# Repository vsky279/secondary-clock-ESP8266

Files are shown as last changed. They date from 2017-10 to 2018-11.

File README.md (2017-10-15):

# Driving secondary clock by ESP8266

Check out this Youtube [video](http://www.youtube.com/watch?v=zKabXwngn9Y) to see the clock in work.

Secondary clock IPJ0612 driven by ESP8266 (http://www.youtube.com/watch?v=zKabXwngn9Y)

## Intro

I have received this beautiful secondary clock [IPJ0612](https://www.pragotron.sk/?ukaz=content/ipj0612) produced by Czech company Pragotron in 80's. Secondary here means that the clock is only a "display" and has to receive signals from a central clock to move by one minute.
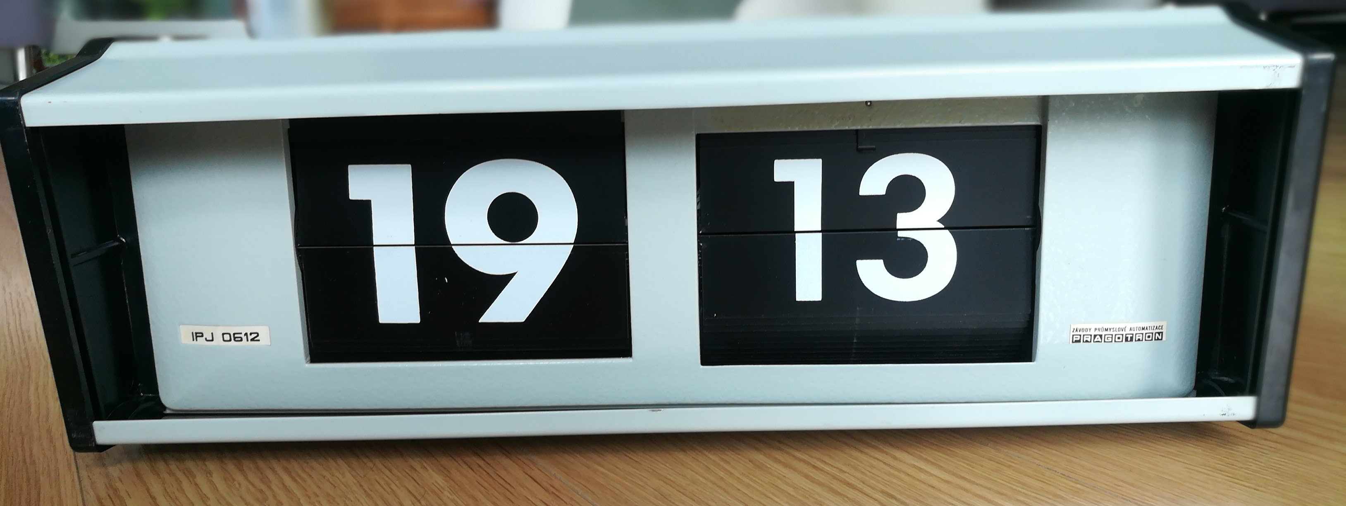
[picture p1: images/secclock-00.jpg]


The clock is driven by kind of a stepper motor, powered by 24V. It has two wires as input directly connected to the coil. For one half turn an impulse of 24V is required for the remaining half turn -24V are applied.
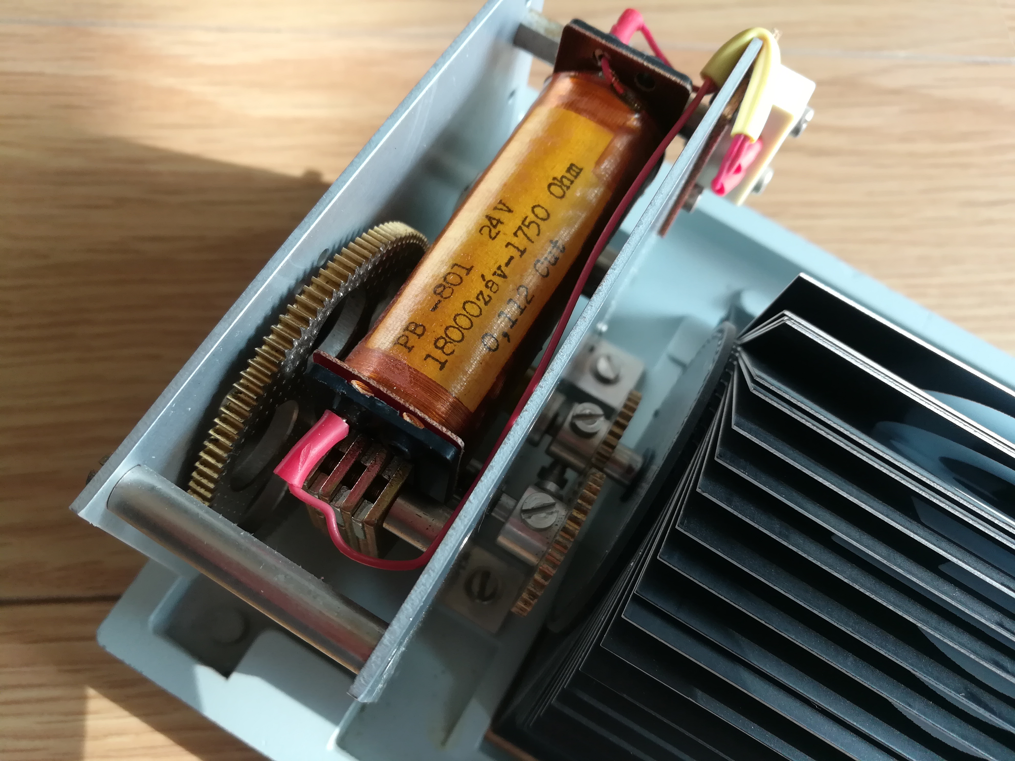
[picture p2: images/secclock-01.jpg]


## Electronics

We needed to use a circuit that can revert the voltage on its output. Two inputs are connected to ESP8266 GPIOs (GPIO0 and GPIO2). GPIO0 set to high makes 24V on output. Setting GPIO2 high causes -24V on output. A pull-up resistors are connected to GPIOs so that ESP8266 boots in desired 'normal operation' mode. A protection transistor (QX on the scheme) for accidental highs on both inputs has been added. The ESP8266 ESP-01 version is used.

We have used Eagle to draw the [scheme](./hw/driver.sch) and design the [board](./hw/board.sch).
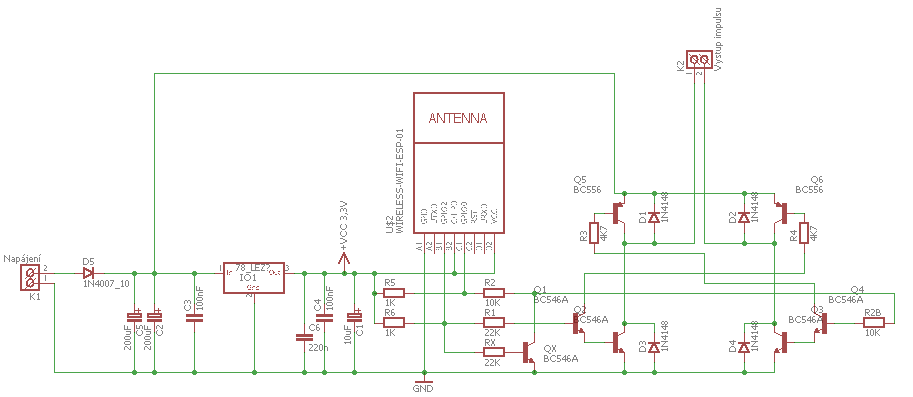
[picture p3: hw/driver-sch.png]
scheme

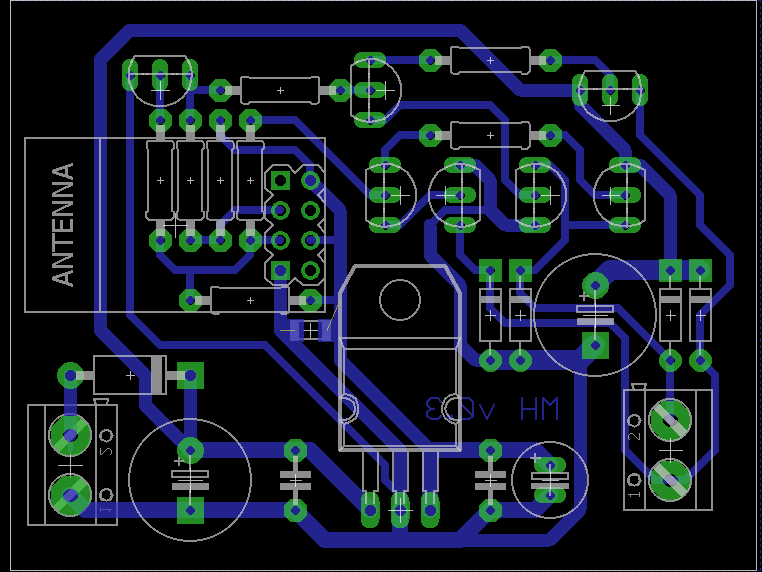
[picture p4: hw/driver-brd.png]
board


To get the 3.3 voltage to power the ESP8266 a LM1085IT-3.3 TO220 regulator is used.
In my implementation, I'm using step-down module as I had one spare at home (the component with annoying blue LED on the pictures below). It's sold on eBay and can be found as [3A 9V/12V/19V To 3.3V DC-DC USB Step Down Buck Power Supply Module For Car](https://www.ebay.com/sch/i.html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). 

## Programming

I am using NodeMCU Lua ([https://github.com/nodemcu/nodemcu-firmware](https://github.com/nodemcu/nodemcu-firmware)) to program the ESP8266. The programming in Lua is very easy so the core program can have less than 140 lines including the web server used to adjust the clock.

A [NodeMCU custom builds](https://nodemcu-build.com/) tool can be used to compile the binary for ESP8266. Beside standard modules the following modules are used: `cron, enduser_setup, rtctime, sntp`. I have used the integer version of the firmware is used. Though float version should be fine too.

I am using [ESP8266 Flasher](https://github.com/nodemcu/nodemcu-flasher) to flash the binary.

To upload Lua files and files used by the web server the [ESPlorer](https://esp8266.ru/esplorer/) GUI can be used.

The program connects to the WIFI, regularly synchronizes time via NTP and sends 300ms to GPIO0 and GPIO1 alternately. To show correct time ESP needs to know what time the clock is showing at startup so it can set it to actual time. This can be adjusted in web browser as the ESP8266 is running a web server. Otherwise the clock assumes correct time is displayed and sends signals as time goes on.

It exposes also a telnet server so an OTA-like update of Lua codes can be performed.

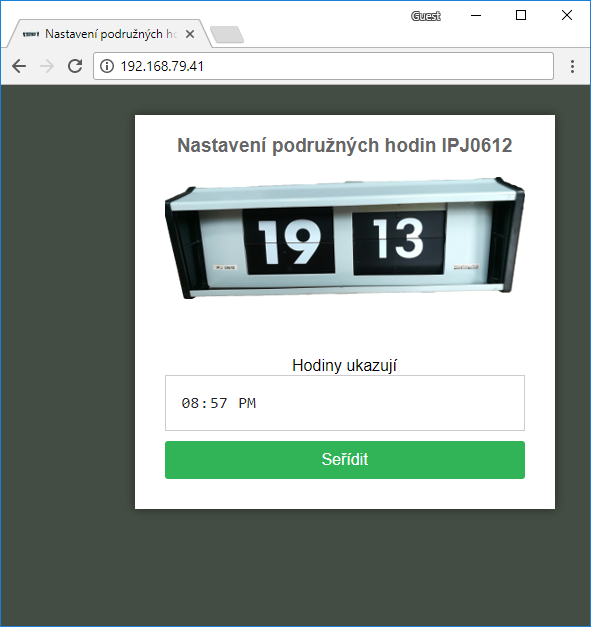
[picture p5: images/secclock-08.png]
web server


In my implementation am using only 18V to run the clock (a power adapter from an old printer). With 24V the signal could probably be shorter than 300ms so clock adjustment would be faster.

The source code is in the folder [lua_code](https://github.com/vsky279/secondary-clock-ESP8266/tree/master/lua_code).

## Assembly

A 3d printed [holder](./holder/holder.skp) (designed in SketchUp) and double face duck tape has been used to mount the board inside the clock. An [STL file](./holder/holder.stl) is usually used in the slicer software.
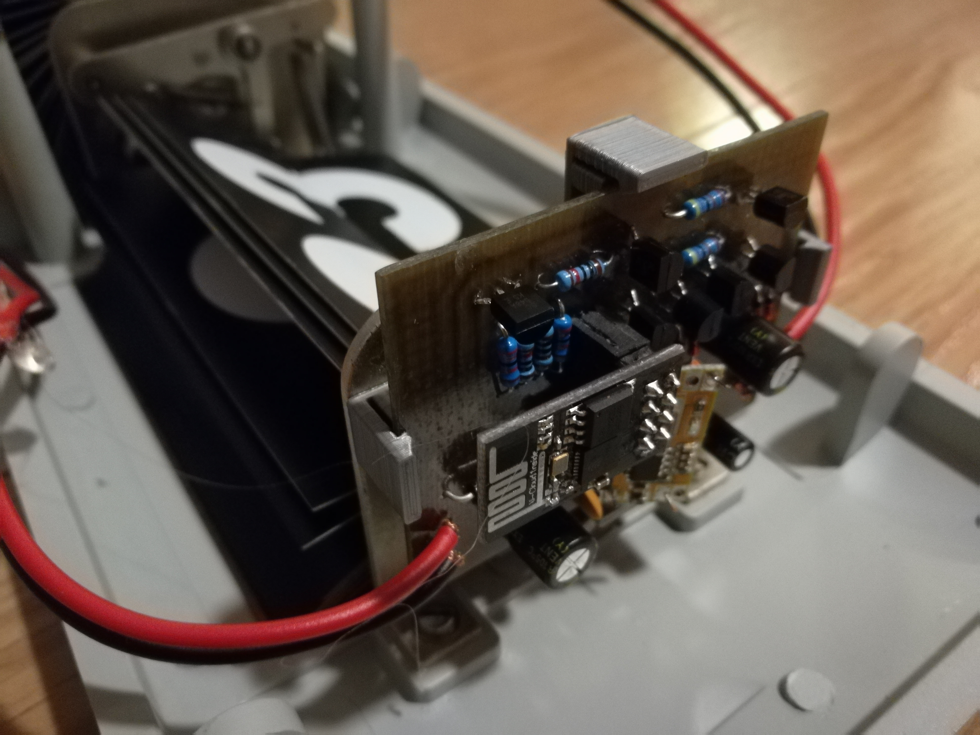
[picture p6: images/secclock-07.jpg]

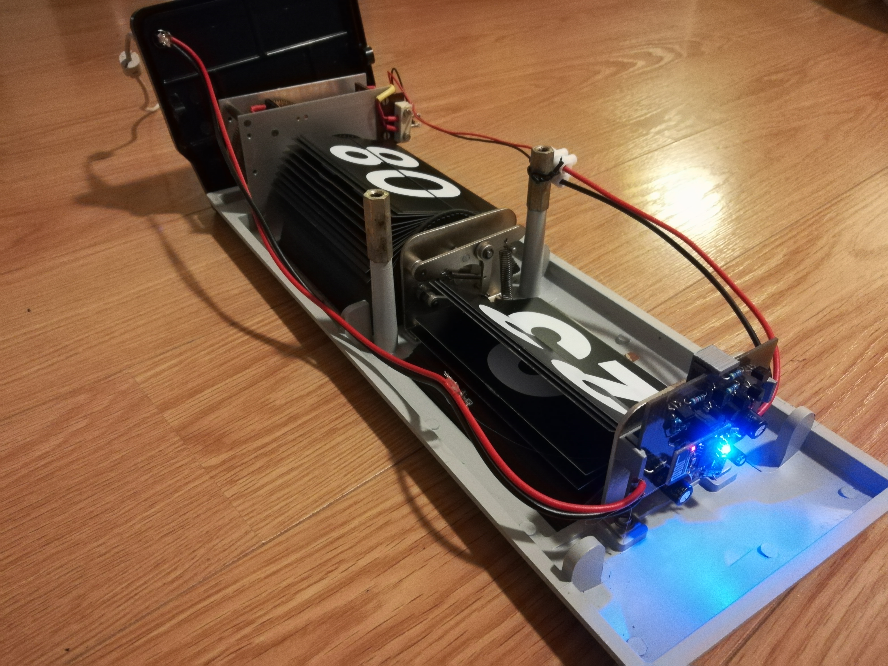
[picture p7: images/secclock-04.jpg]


I have also designed a cap to cover the hole of the original connector ([SketchUp file](./hw/holder/cap.skp) and [STL file](./holder/cap.stl)) - not shown on any of photos.

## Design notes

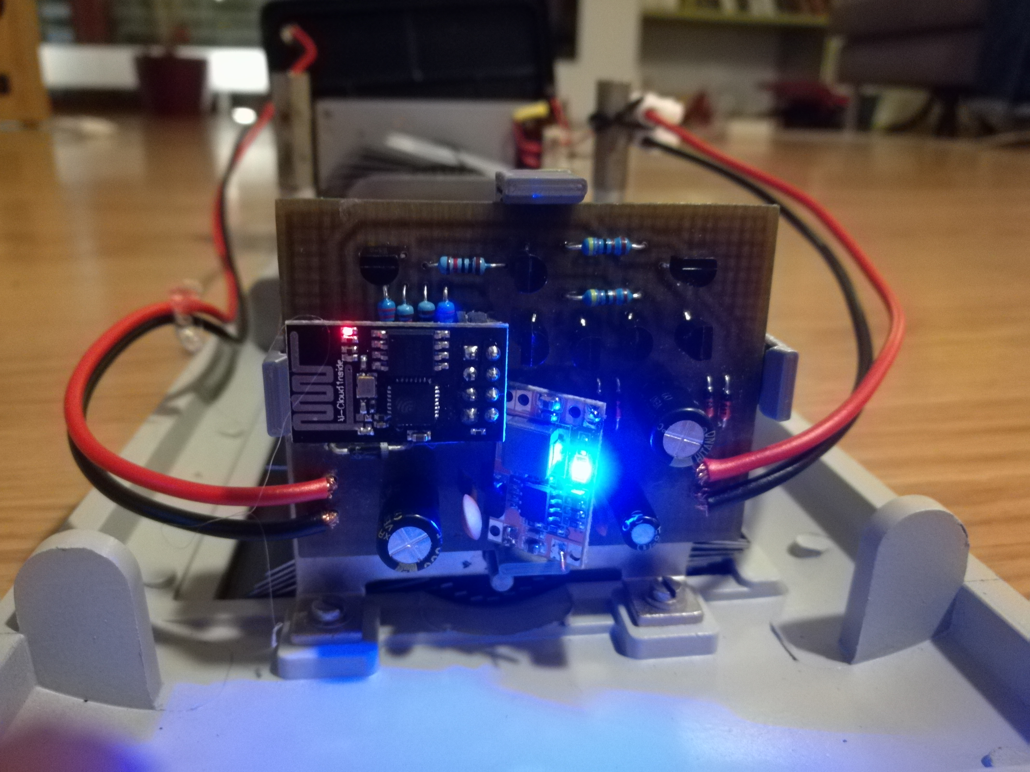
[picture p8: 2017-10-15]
images/secclock-05.jpg

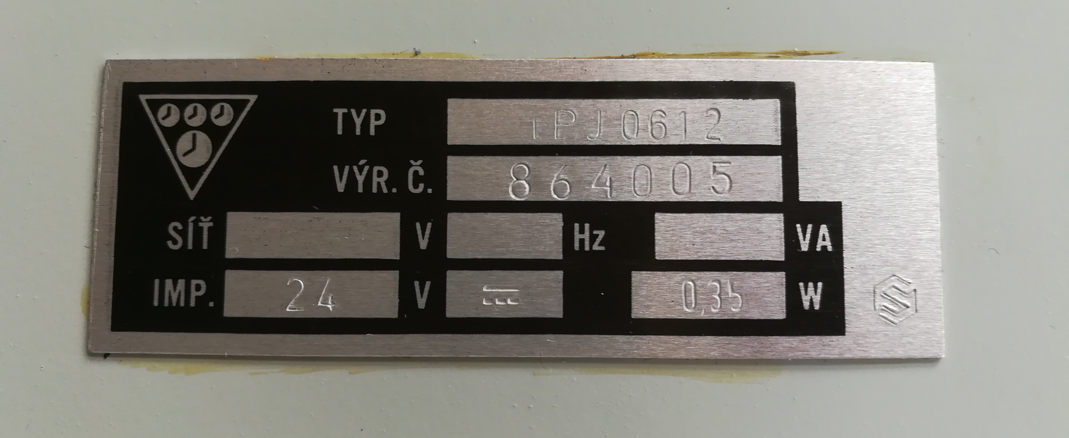
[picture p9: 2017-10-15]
images/secclock-03.jpg

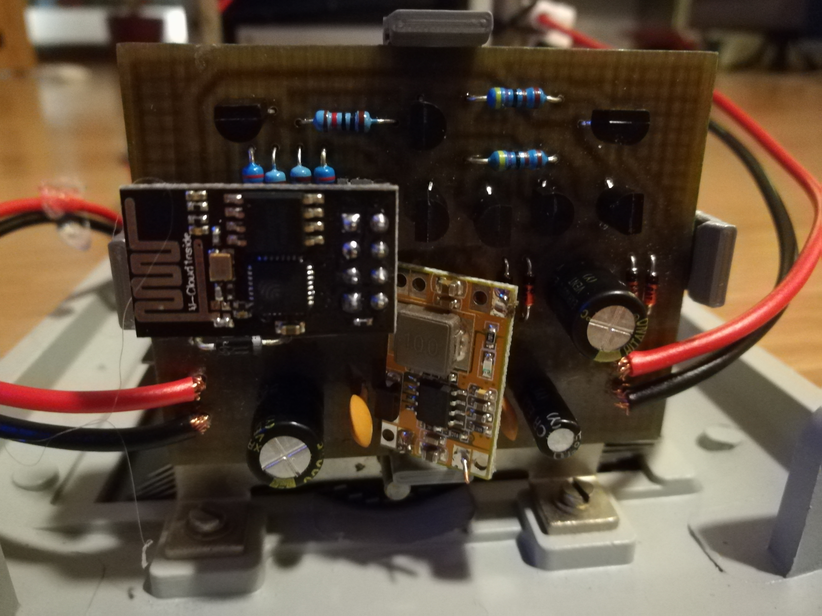
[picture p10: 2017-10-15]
images/secclock-06.jpg

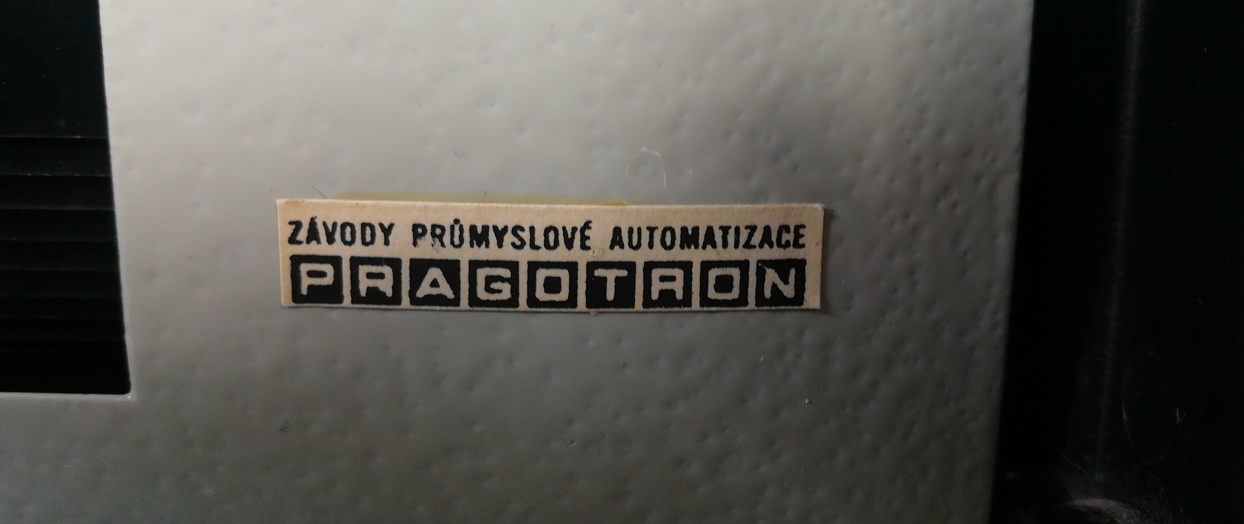
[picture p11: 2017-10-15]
images/secclock-02.jpg

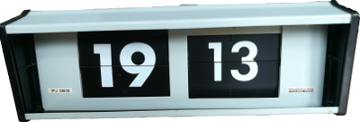
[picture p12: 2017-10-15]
lua_code/src/IPJ_0612-orig.png

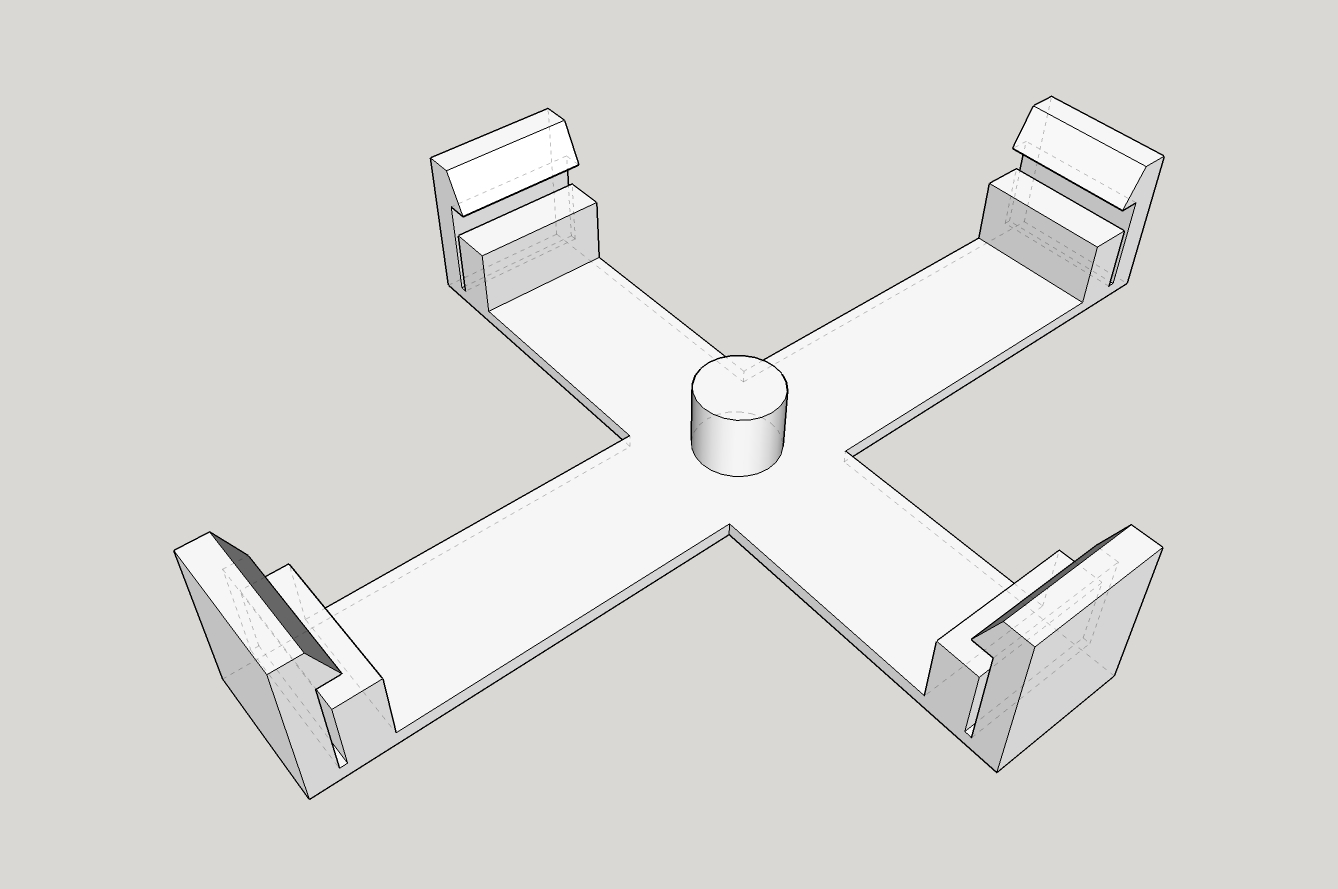
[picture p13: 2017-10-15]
holder/holder.jpg

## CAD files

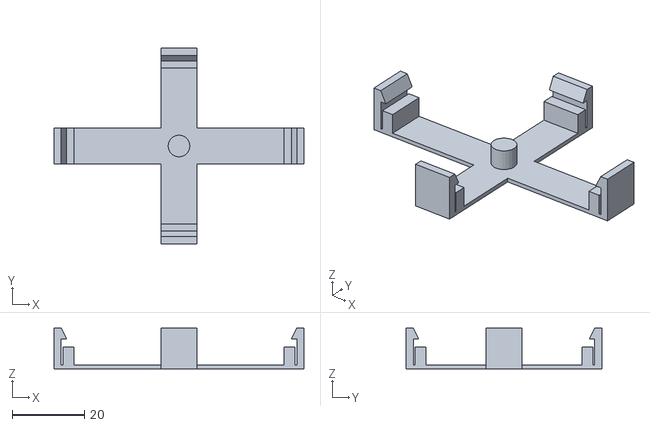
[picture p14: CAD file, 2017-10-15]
holder/holder.stl
69.0 x 54.0 x 11.2

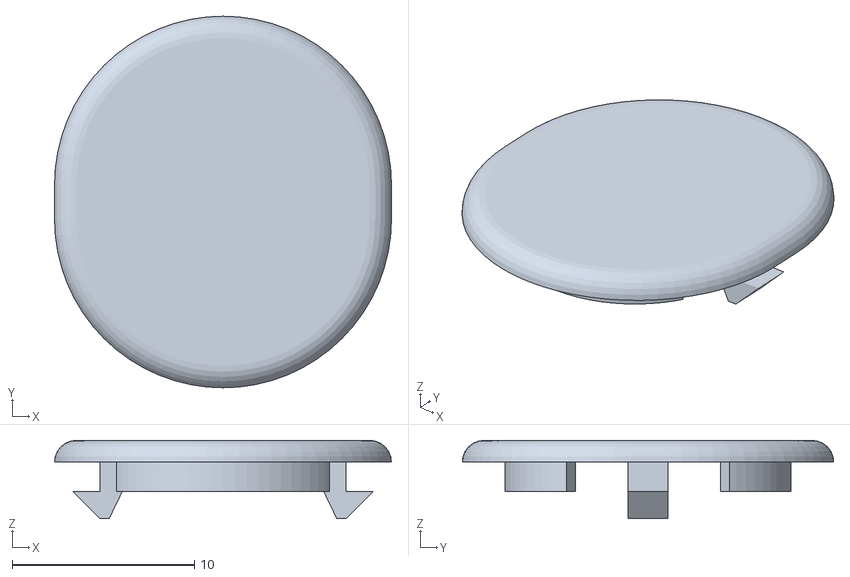
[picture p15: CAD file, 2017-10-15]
holder/cap.stl
18.5 x 20.4 x 4.30

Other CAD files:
holder/cap.skp
holder/holder.skp

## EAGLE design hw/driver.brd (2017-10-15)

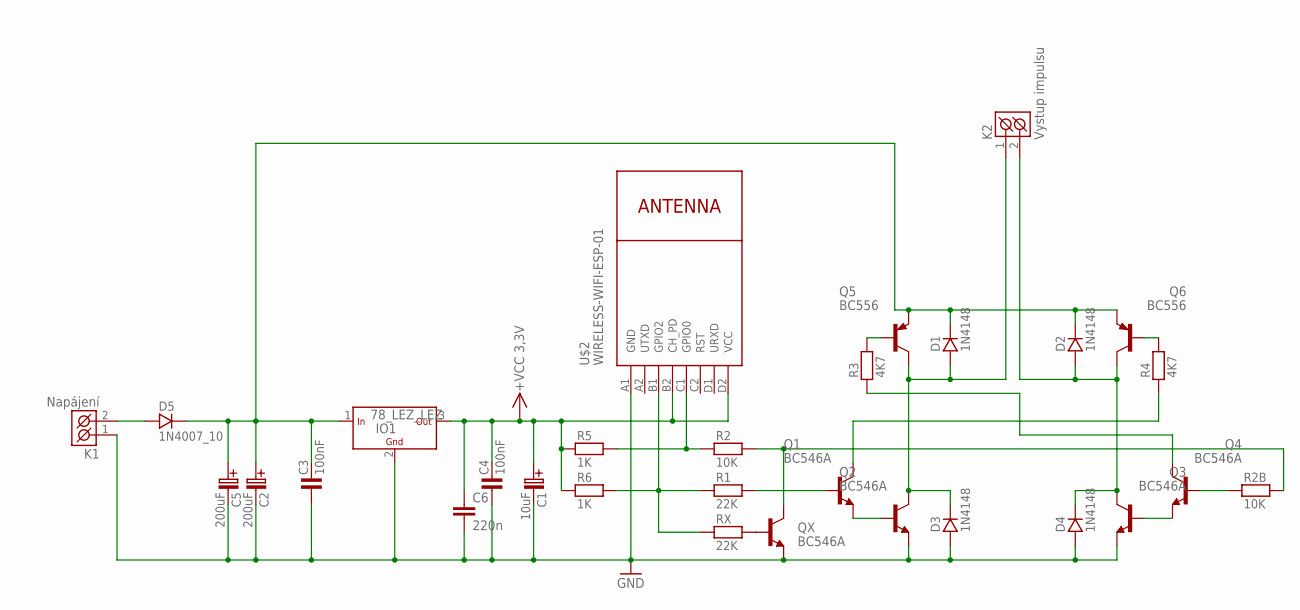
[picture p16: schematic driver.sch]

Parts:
C1: 10uF; C-EL_2,5
C2, C5: 200uF; C-EL_5
C3, C4: 100nF; C-5
C6: 220n; C1206
D1, D2, D3, D4: 1N4148; DO35
D5: 1N4007_10; DO41
IO1: 78_LEZ_LEZ; TO-220
K1: Napájení; CZM_5/2
K2: Vystup impulsu; CZM_5/2
Q1, Q2, Q3, Q4: BC546A; TO92-EBC
Q5, Q6: BC556; TO92-EBC
QX: BC546A; TO92-EBC
R1: 22K; R-10
R2, R2B: 10K; R-10
R3, R4: 4K7; R-10
R5, R6: 1K; R-10
RX: 22K; R-10
U$2: WIRELESS-WIFI-ESP-01

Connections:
GND: C1.C- (C_EL-), C2.C- (C_EL-), C3.1, C4.1, C5.C- (C_EL-), C6.2, D3.A, D4.A, IO1.2 (GND), K1.1 (K1), Q2.E, Q3.E, QX.E, U$2.A1 (GND)
unnamed: D2.A, D4.K, K2.2 (K2), Q3.C, Q6.C
unnamed: D1.A, D3.K, K2.1 (K1), Q2.C, Q5.C
unnamed: C2.C+ (C_EL+), C3.2, C5.C+ (C_EL+), D1.K, D2.K, D5.K, IO1.1 (IN), Q5.E, Q6.E
unnamed: Q5.B, R3.2
unnamed: Q6.B, R4.2
unnamed: Q4.C, R3.1
unnamed: Q1.C, R4.1
unnamed: Q4.B, R2B.1
unnamed: Q3.B, Q4.E
unnamed: Q1.E, Q2.B
unnamed: D5.A, K1.2 (K2)
unnamed: Q1.B, R1.2
unnamed: R1.1, R6.2, RX.1, U$2.B1 (GPIO2)
unnamed: QX.C, R2.2, R2B.2
unnamed: R2.1, R5.2, U$2.C1 (GPIO0)
unnamed: QX.B, RX.2
VCC: C1.C+ (C_EL+), C4.2, C6.1, IO1.3 (OUT), R5.1, R6.1, U$2.B2 (CH_PD), U$2.D2 (VCC)

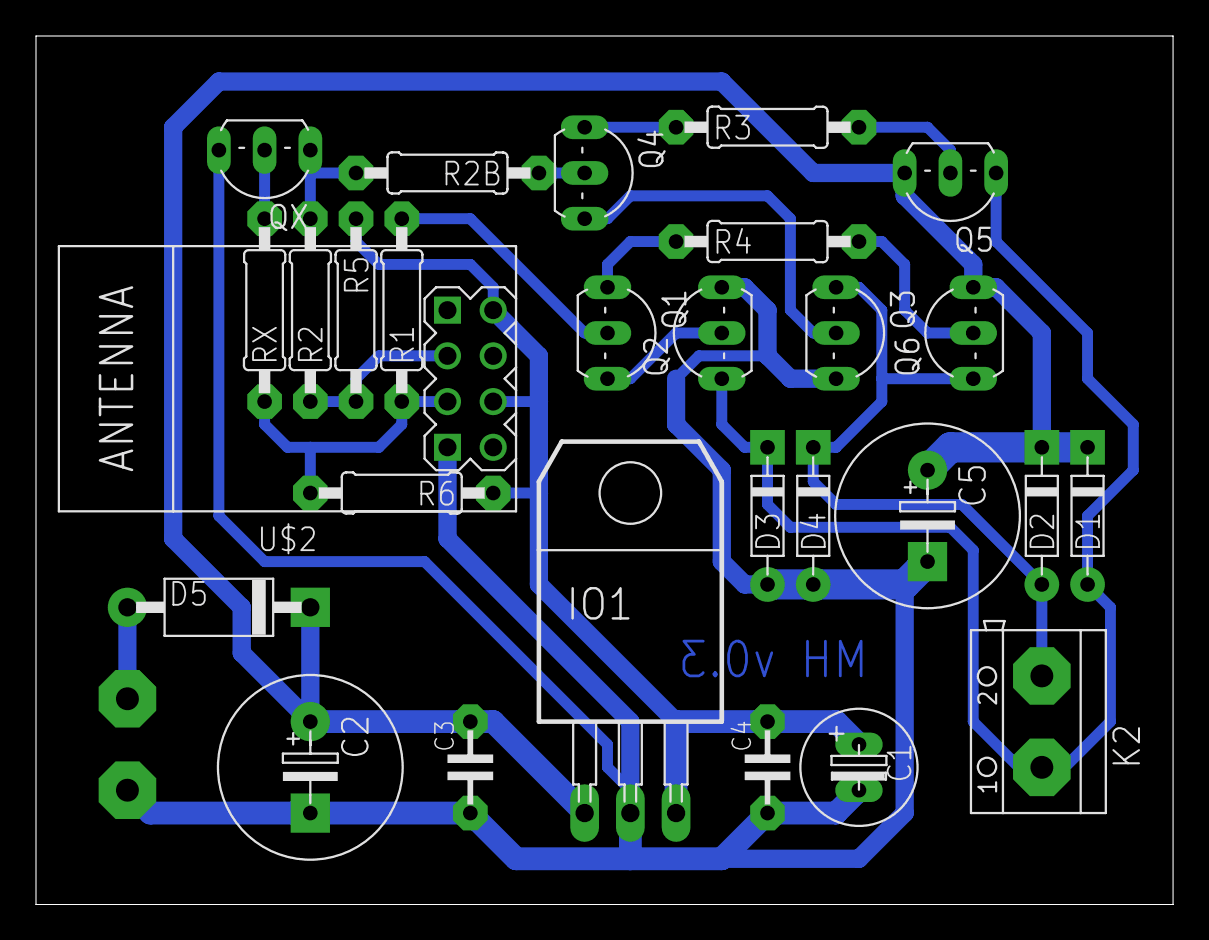
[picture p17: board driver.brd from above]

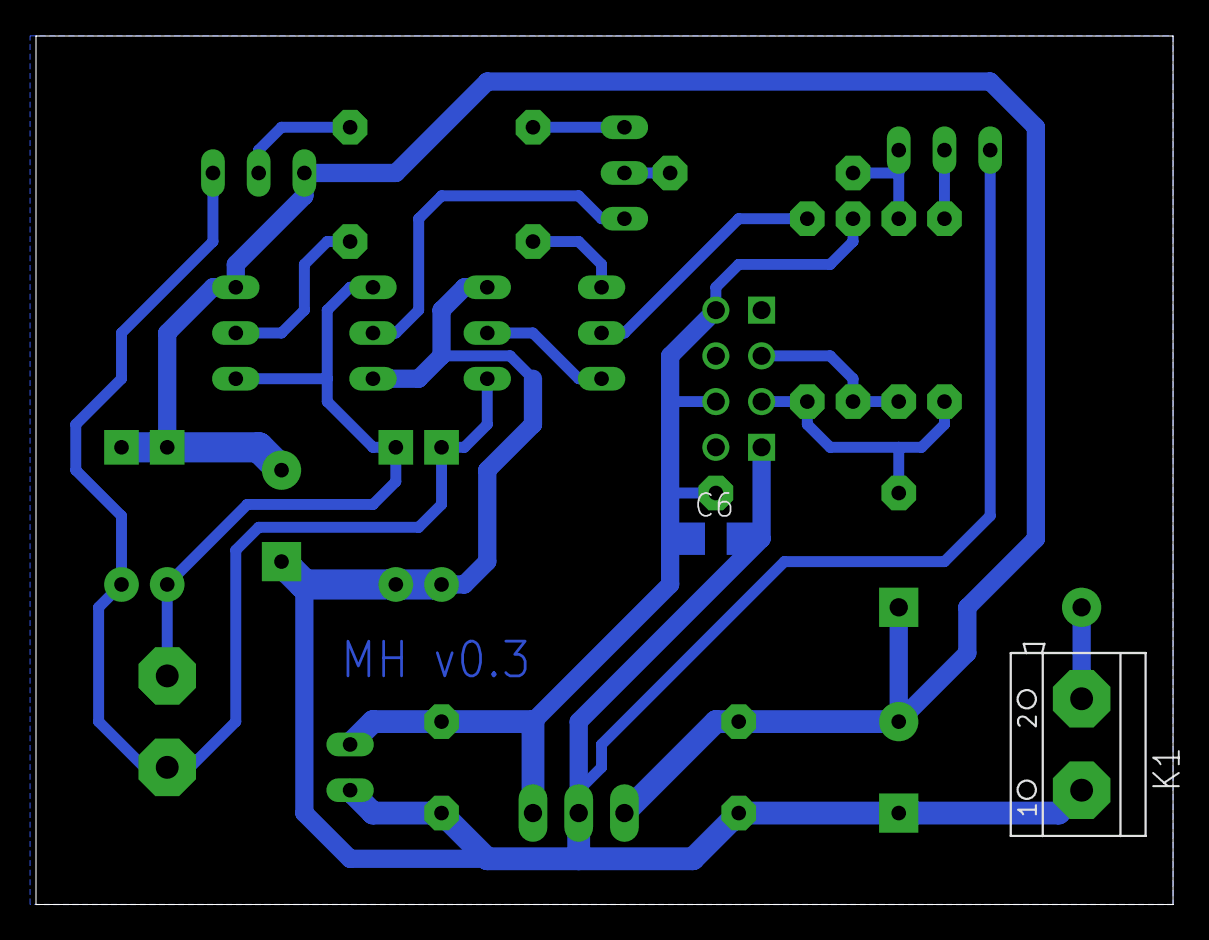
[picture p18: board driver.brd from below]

Board: 2 copper layers, 63.2 x 48.2 mm, 30 parts (2 on the bottom side), 18 nets.

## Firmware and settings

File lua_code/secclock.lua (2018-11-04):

n=require("ntp")

local PIN1 = 3
local PIN2 = 4
local impulse = 300 -- in ms
local delay = 10 -- in ms

local tmr_alarm, tmr_unregister, tmr_ALARM_SINGLE, tmr_ALARM_AUTO, tmr_create, tmr_now = tmr.alarm, tmr.unregister, tmr.ALARM_SINGLE, tmr.ALARM_AUTO, tmr.create, tmr.now
local string_find, string_gmatch, string_format, string_sub, string_gsub = string.find, string.gmatch, string.format, string.sub, string.gsub
local gpio_mode, gpio_serout, gpio_write, gpio_HIGH, gpio_LOW, gpio_OUTPUT = gpio.mode, gpio.serout, gpio.write, gpio.HIGH, gpio.LOW, gpio.OUTPUT

--display == (19*60+15) * 60

local state = true
local tmr_sync = tmr_create()
local tmr_adjust = tmr_create()
local tmr_zero = tmr_create()

gpio_mode(PIN1, gpio_OUTPUT)
gpio_mode(PIN2, gpio_OUTPUT)
gpio_write(PIN1, gpio_LOW)
gpio_write(PIN2, gpio_LOW)

local function display_s()
  local minute = display / 60
  local hour = minute / 60
  minute = minute % 60
  return string_format("%02d:%02d", hour, minute)
end

local last_step = 0
function step()
  local now = tmr_now()
  local dif = now - last_step
  dif = ( (dif < 0) and ((dif + 0x7FFFFFFE) + 1) or dif) /1000 -- workaround for #1691
  if dif < (impulse + delay) then return end

  local pin = state and PIN1 or PIN2
  state = not state
  display = (display + 60) % 86400
  print(string_format("display shows %s, signal on GPIO%d (free mem: %d)", display_s(), pin, node.heap()))
  --gpio_serout(pin, gpio_HIGH, {impulse*1000, delay*1000}, 1, 1)
  gpio_write(pin, gpio_HIGH)
  tmr_alarm(tmr_zero, impulse, tmr_ALARM_SINGLE, function() return gpio_write(pin, gpio_LOW) end)
  last_step = now
end

function adjust()
  local now = n:time() % 86400
  local dif = (now - display) / 60 -- difference in minutes
  if dif < -10 then dif = dif + 1440 end

  print(string_format("display shows %s, time is %s, %d minutes difference (free mem: %d)", display_s(), n:format(now), dif, node.heap()))
  if dif > 0 then
    step()
    dif = dif - 1
    if dif > 0 then
      tmr_alarm(tmr_adjust, impulse + delay, tmr_ALARM_SINGLE, adjust)
    end
  end
end

local cronent
function timeSync()
    n:sync(function ()
      if not display then display = ((n:time() % 86400) / 60) * 60 end
      if not cronent then cronent = cron.schedule("* * * * *", adjust) end
      return tmr_alarm(tmr_sync, 90*60*1000, tmr_ALARM_AUTO, timeSync) 
    end, function() 
      return tmr_alarm(tmr_sync, 10*1000, tmr_ALARM_SINGLE, timeSync) 
    end)
end

timeSync()

srv=net.createServer(net.TCP)
srv:listen(80,function(conn)
  conn:on("receive", function(client, request)
    local _, _, method, path, vars = string_find(request, "([A-Z]+) (.+)?(.+) HTTP")
    if(method == nil)then
        _, _, method, path = string_find(request, "([A-Z]+) (.+) HTTP")
    end
    print("request: ", method, path, vars)
    path = string_sub(path, 2) -- remove first char, i.e. "/"
    local index = (path == "")
    path = index and "index.html" or path
    local fd = file.open(path, "r")
    if not fd then 
        client:send("HTTP/1.0 404 Not Found\r\n\r\n404 Not Found\r\n") 
        return
    end
    if index then
      local _GET = {}
      if (vars ~= nil)then
          for k, v in string_gmatch(vars, "(%w+)=([%w%%]+)&*") do
            _GET[k] = v
          end
      end
      local _GET_time = _GET.time
      _GET = nil
      if(_GET_time) then
        local _, _, hour, minute = string_find(_GET_time, "([0-9]+)%%3A([0-9]+)")
        print(string_format("set time to: %02d:%02d", hour, minute))
        display = hour*3600+minute*60
        adjust()
      end

      local line, content = "", ""
      while line do
          line = string_gsub(line, "$TIME", display_s())
          content = content .. line
          line = fd:readline()
      end
      fd:close()
      if content then 
        client:send(content, function (c) 
          c:close() 
          c:on("sent", nil)
        end) 
      end
    else
      local function sendfile()
        local line=fd:read(1024)
        if line then
          client:send(line, sendfile)
        else
          fd:close()
          client:close()
          client:on("sent", nil)
        end
      end
      sendfile()
    end
  end)
end)

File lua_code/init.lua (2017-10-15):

local fn="secclock"
local smph = "semaphore.tmp"

local tmr_create, tmr_alarm, tmr_ALARM_SINGLE = tmr.create, tmr.alarm, tmr.ALARM_SINGLE

gpio.mode(3, gpio.OUTPUT);
gpio.write(3, gpio.LOW);
gpio.mode(4, gpio.OUTPUT);
gpio.write(4, gpio.LOW);

local function con(t)
  local cred = {your_default_wifi="password"}
  for ssid, _ in pairs(t) do
    if cred[ssid] then
      print("SSID: "..ssid)
      wifi.sta.config({ssid=ssid, pwd=cred[ssid]})
      wifi.sta.connect()
      return
    end
  end
  enduser_setup.start();
end

local function disarm()
    print("disarming semaphore")
    file.remove(smph)
end

print("Setting up WIFI...")
wifi.setmode(wifi.STATION)
wifi.setphymode(wifi.PHYMODE_G)
wifi.sta.getap(con, 1)
tmr_alarm(0,1000,1,function() 
  if wifi.sta.getip()== nil then 
    print("IP unavailable...") 
  else 
    tmr.stop(0)
    print("IP: "..wifi.sta.getip())
    print("Starting "..fn.." in 1 seconds")
        tmr_alarm(0, 1000, 0, function() 
            print("telnet")
            require("telnet")
            if not file.exists(smph) then
                file.open(smph, "w"):close()
                tmr_create():alarm(60000, tmr_ALARM_SINGLE, disarm)
                print(fn)
                require(fn)
            else
              print("semaphore armed - stopping")
              tmr_restart=tmr_create()
              tmr_restart:alarm(600000, tmr_ALARM_SINGLE, function()
                  disarm()
                  node.restart()
              end)
            end
        end)
  end 
end)

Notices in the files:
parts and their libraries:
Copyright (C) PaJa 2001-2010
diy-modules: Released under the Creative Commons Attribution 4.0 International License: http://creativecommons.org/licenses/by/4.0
